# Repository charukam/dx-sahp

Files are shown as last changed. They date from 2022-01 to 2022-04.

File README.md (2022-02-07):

# Direct Expansion Solar Assisted Heat Pump
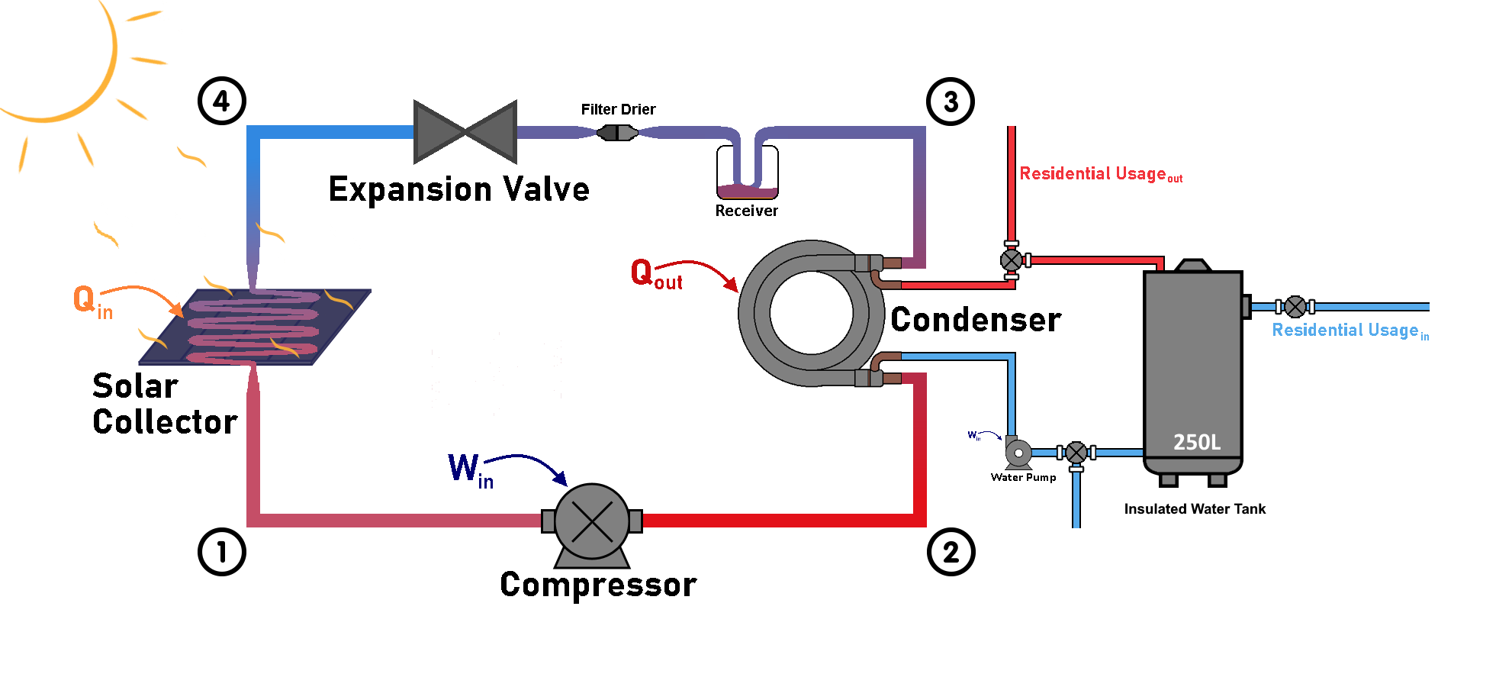
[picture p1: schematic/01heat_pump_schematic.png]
Heat Pump Cycle Schematic

Univeristy of Calgary Capstone Project creating a full scale heat pump cycle with a novel solar collector to heat a domestic hot water tank.

### MATLAB Code
_CoolProp_ (a C++ library) is required to run the MATLAB code to calculate system states for different refrigerants: http://www.coolprop.org/

### SOLIDWORKS Model
SOLIDWORKS 2020 is required for the SLDPRT and SLDASM files

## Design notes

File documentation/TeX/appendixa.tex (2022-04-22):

\chapter{Appendix A: Bill of Materials}

\begin{figure}[H]
    \centering
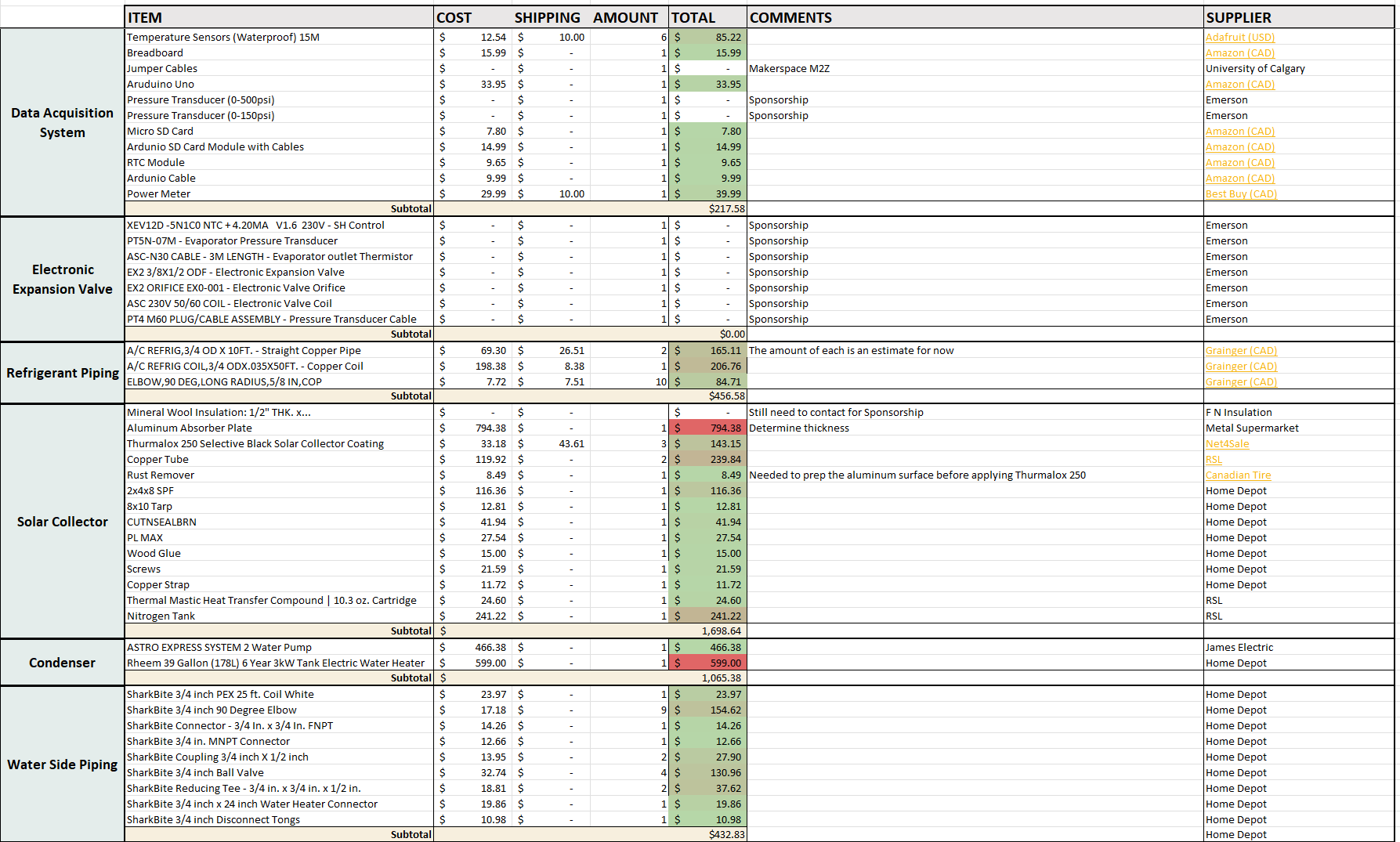
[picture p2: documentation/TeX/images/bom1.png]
    
\end{figure}
\begin{figure}[H]
    \centering
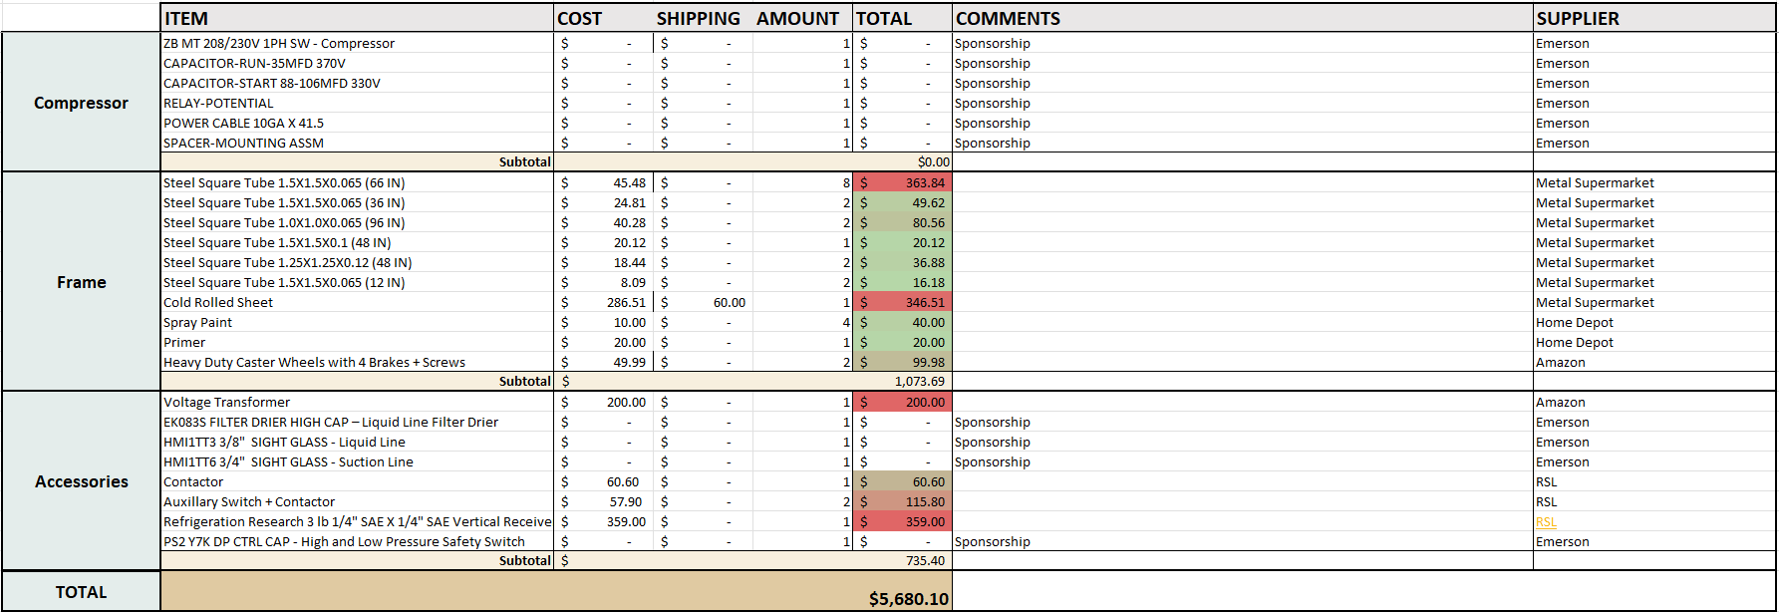
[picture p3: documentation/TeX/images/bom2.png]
    
\end{figure}

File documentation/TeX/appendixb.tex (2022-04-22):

\chapter{Appendix B: Gantt Chart}

\begin{figure}[H]
    \centering
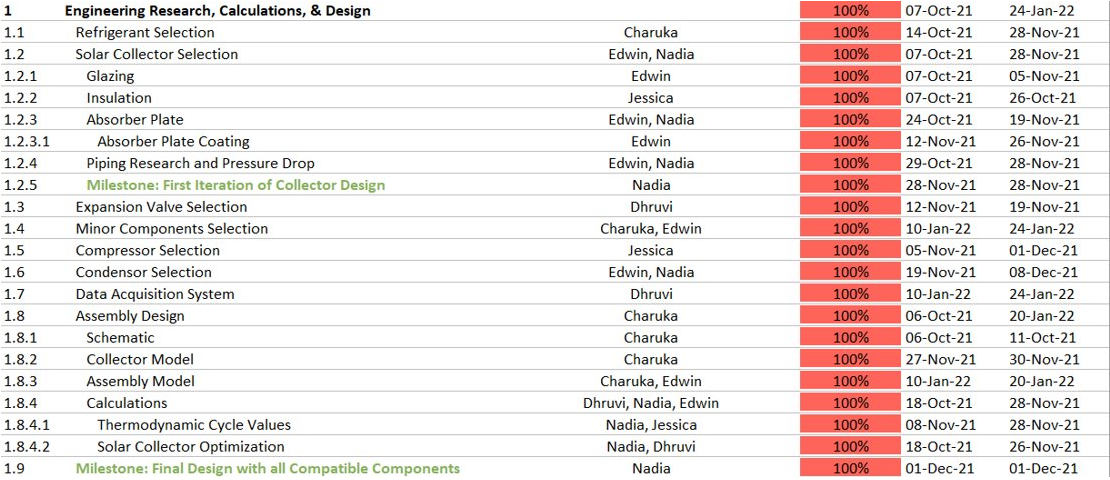
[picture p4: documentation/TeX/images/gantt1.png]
    
\end{figure}
\begin{figure}[H]
    \centering
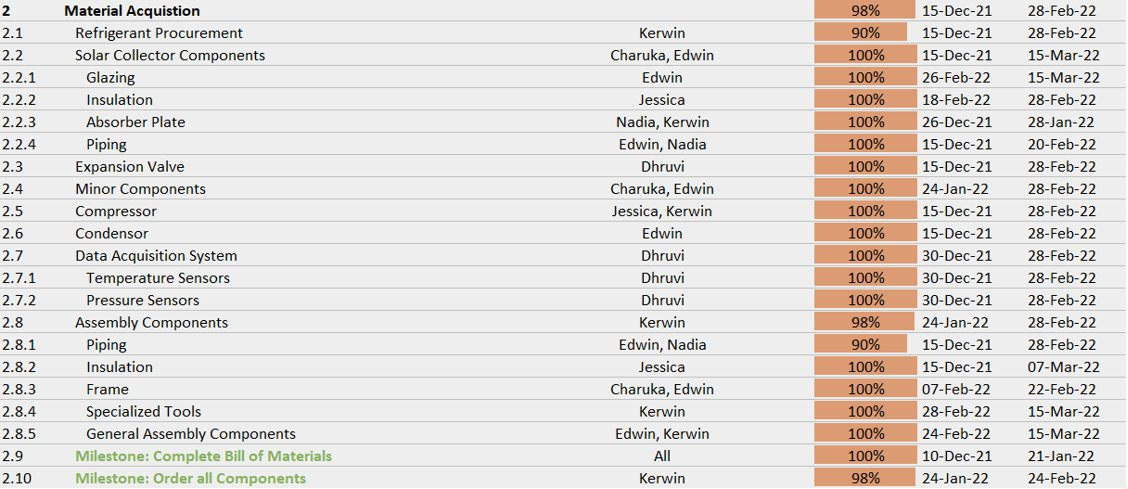
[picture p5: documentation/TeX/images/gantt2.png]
    
\end{figure}
\begin{figure}[H]
    \centering
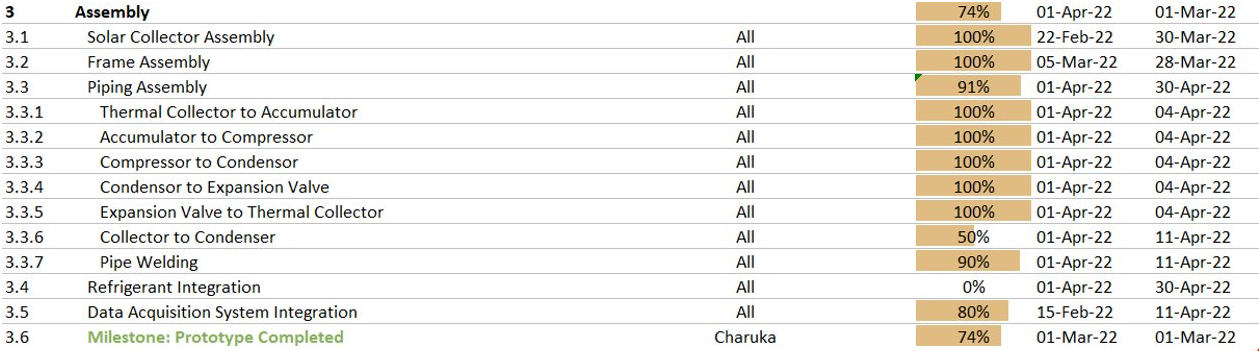
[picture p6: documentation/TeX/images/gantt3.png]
    
\end{figure}
\begin{figure}[H]
    \centering
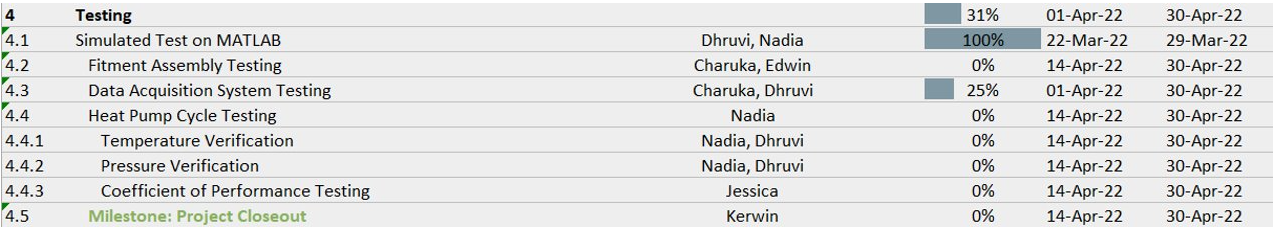
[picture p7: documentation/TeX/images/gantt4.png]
    
\end{figure}

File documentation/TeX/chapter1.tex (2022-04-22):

\chapter{Project Overview}

\section{Background and Motivation}

Climate change is a growing concern due to the effects that global warming has on the environment. As the population of the world increases, the energy demand will increase in turn. Due to the reliance on fossil fuels, this will only increase the amount of greenhouse gases that is produced into the atmosphere. This is why it is important to explore alternative energies that are relatively “greener” in comparison to the standard fossil fuels that are mainly used.

\medskip
A major sector where energy can be saved is domestic hot water heating. 19.3\% of the residential energy usage in Canada is from water heating \cite{water_heaters}. This statistic can be improved with the implementation of technology that uses other sources of energy to provide water heating. This project focuses on a Direct Expansion Solar Assisted Heat Pump (DX-SAHP), which is an example of a technology that can be used in place of natural gas for heating. The DX-SAHP combines the benefits of a heat pump with the abundance of solar energy that we receive.

\medskip
Unlike an Air Source Heat Pump (ASHP), the DX-SAHP uses a combination of solar energy and the ambient temperature to evaporate the refrigerant, improving the performance and making it viable for areas with a colder climate. The use of solar energy in conjunction with the heat pump reduces the amount of electricity that is needed for a standard heat pump to generate hot water.

\newpage
\begin{figure}[ht]
    \centering
    
    \caption{DX-SAHP Schematic}
\end{figure}
\medskip
The solar collector is what will be used instead of a traditional evaporator in the DX-SAHP. The collector is heated up, due to it being in direct sunlight, and thus it heats up and evaporates the refrigerant running below it. Ambient temperatures play a critical role in the performance of a heat pump with a solar collector. This is due to the solar collector directly being affected by how much irradiance, the amount of light striking a surface, is available. To design a collector for colder climates, where perhaps less irradiance is available, there must be key considerations that are considered. Additionally, other required components must be matched to the demand and to the solar collector size.

\section{Problem Statement}
The current state of heating in Alberta is overly reliant on natural gas and the technology that is currently being used to heat domestic water is contributing to the increase in global temperatures via greenhouse gas emissions. DX-SAHP can be used to phase out natural gas heaters by using the sun as an energy source instead. Therefore, a DX-SAHP can be designed that can heat an average household of 3 people within the Calgary region.

\section{Overview of Scope}
The goal of this capstone is to design a DX-SAHP that can heat 225L of domestic hot water to a household of 3 people. This number was calculated from the information from the Government of Canada stating that the average Canadian uses 75L of hot water a day \cite{water_heaters}. Knowing this, a DX-SAHP will be designed and manufactured. The effort will be mainly focused on optimizing the area of the collector while reducing the heat losses from convection and radiation. Component matching analysis and selecting a compatible compressor, condenser, and electronic expansion valve is necessary so that it is system functions properly. This heat pump must be equipped with all the necessary controls and data acquisition systems. Afterwards a working model will be made in order to be functional within Calgary and an economic and environmental analysis will be conducted to justify the proposed system.

\medskip
To determine the sizing of the DX-SAHP initial parameters must be set.

\medskip
Statistics Canada states that the average Canadian household occupies 2.47 members, and the average Canadian uses 75L of hot water per day \cite{stats_canada}. For the purposes of the DX-SAHP, it will be assumed that a domestic household of 3 people will require 225L of hot water per day. The hot water will be required to exit the system at a temperature of 50\textdegree C for residential use to avoid bacteria buildup in the water tank such as legionella. 

\medskip
The municipal water supply differs in temperature depending on the time of year. When it is winter, municipal line comes in at 10\textdegree C unlike in the summer when it comes in at 20\textdegree C. This is an important parameter to be considered when quantifying what heat load the heat pump will have to supply.

\medskip
To validate and maintain quantifiable design goals, the project will be considered successful if it is able to sustain 225L of water at 50\textdegree C while maintaining a coefficient of performance ($COP$) greater than 2.3. This means the DX-SAHP must be able to provide the following heat loads.

\smallskip
\begin{align}
    Q_L = 225L \times \frac{1000g}{1L} \times 4.18\frac{J}{g\SI{}{\celsius}}\times (\SI{50}{{\celsius}} - \SI{10}{{\celsius}}) = 37,620kJ
    \\\eqname{Heat Load Required during Winter Conditions}
\end{align}

\begin{align}
    Q_L = 225L \times \frac{1000g}{1L} \times 4.18\frac{J}{g\SI{}{\celsius}}\times (\SI{50}{\celsius} - \SI{20}{\celsius}) = 28,215kJ
    \\\eqname{Heat Load Required during Summer Conditions}
\end{align}

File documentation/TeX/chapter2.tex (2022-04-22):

\chapter{Conceptual Design}

\section{Background Research}

The most common water heater is the storage tank water heater. The way it functions is by heating up water that will be stored within a storage tank. This is most conventional since it is easy and cheap to install when comparing it to other water heaters. The limiting factor is that it is limited by the size of the storage tank. It may take a while for the hot water to be heated again if it runs out.

\medskip
Another type of water heater that is used is an Air Source Heat Pump (ASHP). What makes this heat pump unique is that it uses the heat within the air to heat the water. All it needs is a little bit of electricity to power the system. This makes the ASHP two to three times more efficient than most water heaters \cite{heat_pump_water_heaters}. The major drawback is that it needs to take heat from the air, therefore it is not suitable for basements or colder climates.

\begin{figure}[ht]
    \centering
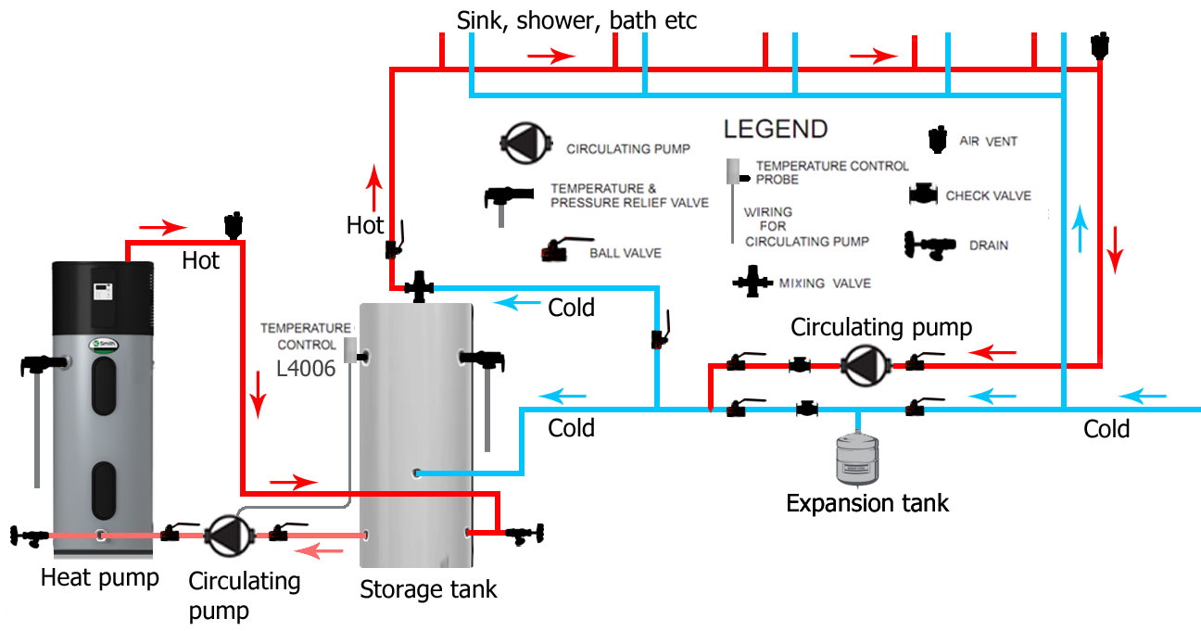
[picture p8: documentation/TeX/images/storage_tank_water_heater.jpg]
    \subfloat[\centering Storage Tank Water Heater {\cite{water_heater_img1}}] {{}}
    \qquad
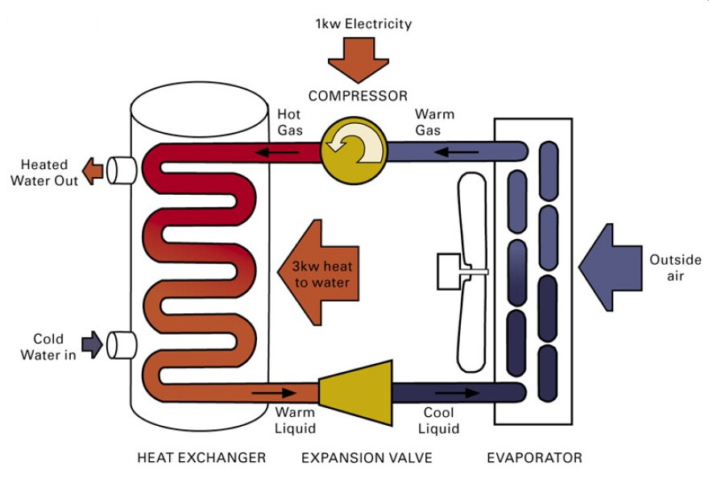
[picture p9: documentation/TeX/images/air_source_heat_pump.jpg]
    \subfloat[\centering Air Source Heat Pump Water Heater {\cite{water_heater_img2}}] {{}}
    \caption{Conventional Water Heaters}
\end{figure}

\smallskip
Unlike the ASHP, the DX-SAHP uses solar energy to provide the heat needed to heat the water. When comparing Figure 2.2 with Figure 1.1, a solar collector is used instead of an evaporator. This gives all the benefit of an Air Source Heat Pump with the additional benefit of working in colder climates since the sun can provide enough energy to heat the water.

\medskip
When designing a DX-SAHP, it is important to consider the irradiance available in the area. Irradiance is the amount of energy received from the sun within an area. As seen in Table 1, the amount of sun Calgary receives is drastically different between the winter and summer data sets.

\medskip
Winter months are defined from October to March in Table 2.1 while summer is between April to September. The justification behind choosing those date ranges is that it makes use of the entire year, and it is split between when Calgary has the most daylight hours versus the least. It also happens to line up with the solstices.

\medskip

\begin{table}[H]
\centering
\caption{Calgary Irradiance Data}
\rowcolors{2}{gray!20}{white}
\begin{tabular}{|P{10mm}|P{70mm}|P{70mm}|}
    \hline
    \rowcolor{orangeRed}
    Hour &  Average Winter Irradiance Data $(W/m^2)$ & Average Summer Irradiance Data $(W/m^2)$ \\
    \hline
    1 & 0 & 0 \\
    2 & 0 & 0 \\
    3 & 0 & 0 \\
    \cite{heat_pump_water_heaters} & 0 & 0 \\
    5 & 0 & 1.398907104 \\
    6 & 0 & 12.99453552 \\
    7 & 0.510989011 & 76.3715847 \\
    8 & 7.736263736 & 182.0710383 \\
    9 & 54.40659341 & 327.442623 \\
    10 & 149.6538462 & 445.6065574 \\
    11 & 229.7857143 & 557.2896175 \\
    12 & 289 & 612.0601093 \\
    13 & 316.7087912 & 629.9289617 \\
    14 & 301.6868132 & 587.7923497 \\
    15 & 252.4285714 & 539.8196721 \\
    16 & 178.3241758 & 474.3715847 \\
    17 & 86.85714286 & 374.3879781 \\
    18 & 29.04395604 & 252.4043716 \\
    19 & 3.708791209 & 142.9016393 \\
    20 & 0 & 44.86885246 \\
    21 & 0 & 4.256830601 \\
    22 & 0 & 0 \\
    23 & 0 & 0 \\
    24 & 0 & 0 \\
    \hline
\end{tabular}
\end{table}

\medskip
\section{Sponsor Requirements}
The sponsor's requirement for this capstone project was the design of a  DX-SAHP system that can satisfy the domestic hot water demand of the average Canadian household (~225L) of hot water per day \cite{stats_canada}.The system had to be disassemble, which was considered through the fabrication of a 3-part support frame, and through the incorporation of valves between the HVAC subcomponents. 

\medskip
\section{Collector Type Selection}

There are three types of solar collectors that are commonly used in the market; they are flat plate collectors, evacuated tube collectors, and concentrating collectors. Each comes with their own benefits and drawbacks.

\medskip
Flat plate collectors consist of a flat absorber plate that is orientated towards the sun. They use both direct and diffuse solar radiation and normally do not require a tracking system. Their main applications are solar water heating, heating for buildings, air conditioning and heat for industrial processes \cite{solar_thermal_energy}.

\medskip
In contrast, evacuated tube collectors consist of several rows of parallel transparent glass tubes which have the working fluid flowing within it. The glass tubes are cylindrical in shape which results in the sunlight always being perpendicular to the heat absorbing tubes. This is a major benefit since this collector can be used when the sun is low in the sky or on cloudy days and they are particularly useful in colder climates.

\medskip
Concentrating collectors are more suited for systems that require higher temperatures than what is achievable with a flat collector. The concentrating collector can be optimized by decreasing the area of heat loss when comparing it to flat plate collectors. This is done by placing an optical device between the source of radiation and the surface. A disadvantage that this technology has is that a sun tracking system is required to always maximize the incident radiation. This tracking system increases the overall cost of the collector and leads to additional maintenance which is why it was not considered at all for this project \cite{solar_thermal_energy}.

\medskip
When comparing flat plate collectors with evacuated tubes, there are several categories that can be considered. When comparing costs, evacuated tubes are around 10-15\% more expensive than flat plate. This was important to consider due to the limited budget that this project has \cite{flat_plate}. Another important area that needs to be looked at would be how the collector can handle snow. Since there will be no tracking system for our design, there will be no way to shake off the snow, so the collector must remove it passively. The benefit of a flat plate collector is that snow can shed easily unlike with evacuated tubes in which it can get stuck due to the tubes creating a strong vacuum \cite{flat_plate}.

\medskip
Both flat plate and solar collectors are excellent at heating water. The main question that needs to be asked when selecting the collector type is how much water needs to be heated to the desired temperature. Evacuated tubes are great for colder climates since they can heat water up to 121\textdegree C but it has the tendency to overheat. Therefore, evacuated tubes are more commonly used for commercial rather than domestic purposes. Unlike evacuated tubes, flat plate collectors can heat water up to 82\textdegree C which means that it is has smaller chance of overheating. This temperature range is suitable for domestic hot water usage \cite{flat_plate}.

\medskip
When looking at all the parameters, the flat plate collector was selected instead of the evacuated tube or concentrating collector. Although the evacuated tube collector works better in colder climates than the flat plate collector, it was excessive in terms of both cost and design work for domestic water heating. The flat plate satisfies many requirements for a collector in colder climates, and it is the recommended collector for domestic water heating \cite{flat_plate}. Therefore, for the design, the flat plate collector was chosen.

\section{Refrigerant Selection}

A refrigerant is a working fluid used in the thermodynamic cycle of a heat-pump, where the fluid will undergo multiple phase changes from liquid to vapor and vice versa, throughout the system cycle. One of the first components in a heat pump, which must be determined early on, is the refrigerant. To determine which components (i.e., compressor, condenser, and expansion valve) will be used in the DX-SAHP, the working fluid must be selected. Although there were many refrigerants to choose from, the list was drastically cut down after considering multiple criteria. These criteria looked at the environmental acceptability, safety, application, performance, and the economics associated with various refrigerants.

\medskip
The Ozone Depletion Potential (ODP) is a measure of a refrigerant’s ability to damage the ozone layer relative to CFC-11 with an ODP of 1. Emissions from CFC’s (chlorofluorocarbons), HCFC’s (hydrochlorofluorocarbons), and other synthetic chemicals which created an “ozone hole” over the South Pole \cite{ozone_layer} have led to the Montreal Protocol on Substances that deplete the Ozone layer \cite{odp} – a global agreement made to phase out ozone-depleting substances. For the DX-SAHP, only refrigerants with an ODP equal to zero were considered.

\medskip
The Global Warming Potential (GWP) is the next major criterion regarding environmental acceptability. This is a metric measuring the energy of emissions, which one ton of a specific gas will absorb relative to the emissions of one ton of carbon dioxide (\ch{CO2}) over a hundred-year period \cite{gwp}. For example, a refrigerant with a GWP of 1430 will have 1430 times the global warming potential of \ch{CO2} over 100 years. In 2016, the Kigali amendment was made to the Montreal Protocol \cite{montreal_protocol}, proposing a complete phase down of HFCs by 2047 due to their high global warming potential. Furthermore, the European Union \cite{hfcs} took action to place market prohibitions on gases with a GWP greater than 750 in air-conditioning systems by 2025. Therefore, the considered refrigerants had to have a GWP below 750.

\medskip
Refrigeration cycles have three distinct applications: high temperature (comfort conditioning), medium temperature (food refrigeration), and low temperature (transport refrigeration). Domestic water heating falls into high temperature comfort conditioning applications. The most widely used refrigerant in these applications has been R-134A and R-134A. Due to the high SEER (Seasonal Energy Efficiency Ratio) ratings of R-134A compared to other refrigerants, it, along with R-410A, has dominated the air conditioning market for components. However, due to R-134A’s high GWP of 1430, refrigerants with similar thermodynamic properties used as replacements for the eventual phase down of R-134A were explored.

\newpage
Following the ASHRAE Standard 34 refrigerant safety classification, most refrigerants in use currently pose a very low toxicity and flammability threat – giving an ASHRAE safety designation of A1. Following the ASHRAE Standard 34 \cite{ashrae_safety} refrigerant safety classification, most refrigerants in use currently pose a very low toxicity and flammability threat – giving an ASHRAE safety designation of A1. ASHRAE Standard 34 assigns refrigerants to two toxicity (A or B), and four flammability classes (1, 2, 2L, 3). The safety designations for refrigerants are as follows:

\begin{itemize}[itemsep=3mm, parsep=-1mm]
\item Class A (Low Toxicity)
    \begin{itemize}
        \item Occupational exposure limit is 400ppm or greater
    \end{itemize}
\item Class B (High Toxicity)
    \begin{itemize}
        \item Occupational exposure limit is less than 400ppm.
    \end{itemize}
\item Class 1 (No flame propagation)
    \begin{itemize}
        \item No flame propagation at 60\textdegree C and atmospheric pressure.
    \end{itemize}
\item Class 2L (Low flammability)
    \begin{itemize}
        \item Flame propagation at 60\textdegree C and atmospheric pressure.
        \item Lower Flammability Limit $> 0.10kg/m^3$ and Heat of Combustion $< 19,000 kJ/kg$
        \item Burning velocity <= 10cm/s at 23\textdegree C
    \end{itemize}
\item Class 2 (Flammable)
    \begin{itemize}
        \item Flame propagation at 60\textdegree C and atmospheric pressure.
        \item Lower Flammability Limit $> 0.10kg/m^3$ and Heat of Combustion $< 19,000 kJ/kg$
    \end{itemize}
\item Class 3 (High flammability)
    \begin{itemize}
        \item Flame propagation at 60\textdegree C and atmospheric pressure.
        \item Lower Flammability Limit $<= 0.10kg/m^3$ or Heat of Combustion $< 19,000 kJ/kg$
    \end{itemize}
\end{itemize}

\medskip
Because the system was designed for a residential water heating supply, only refrigerants designated in Class A toxicity were used due to possibility of leakage.

\medskip
As with many design considerations in engineering, there is an equivalent exchange when reducing the global warming potential of refrigerants. A general trend can be observed in refrigerants where a lower GWP equates to a higher flammability designation; most new generation refrigerants with a GWP less than 750 have an ASHRAE safety designation of A2L. While refrigerants of Class 1 are the most desirable, Class 2L refrigerants can also be considered safe \cite{low_gwp} to use in domestic heating systems as they have a high Minimum Ignition Energy and would need to be exposed to an open flame or high energy source with sufficient concentrations to ignite.

\medskip
Although each refrigerant will result in different system efficiencies, by looking at the critical temperature of the refrigerant, a correlation can be made for both the coefficient of performance and the cooling capacity of the system. As the critical temperature of the refrigerant increases, the coefficient of performance of the system is found to increase, while the cooling capacity is found to decrease \cite{low_gwp_options}. A higher coefficient of performance will ultimately result in a lower energy bill for the end user, while a lower cooling capacity will result in a larger system. As the project location is for a cold climate in Calgary, the refrigerant must also be chosen to have a freezing point, $T_{fp} < \SI{-50}{\celsius}$. Furthermore, CoolProp \cite{cool_prop} was used to conduct the thermodynamic analysis, and therefore, refrigerants of choice must be available on the database such that the system calculations can be performed.

\medskip
Finally, the economics and procurement of the refrigerants were considered where the system will require between 3-6 pounds of charge. After contacting vendors, many refrigerants were found to have more than 3 months lead times due to COVID-19 supply chain issues, and as a result would not satisfy the project’s timeline. Many new generation refrigerants were also found to be cost-ineffective when compared to their incremental performance benefits. These refrigerants ranged from \$400 to \$3000 per their minimum selling quantities.

\medskip
A design requirements table was then created to easily compare the refrigerants as seen below.

\medskip
\begin{table}[H]
\centering
\caption{Refrigerant Criteria}
\rowcolors{2}{gray!20}{white}
\begin{tabular}{|P{23mm}|P{23mm}|P{23mm}|P{23mm}|P{23mm}|P{23mm}|}
    \hline
    \rowcolor{orangeRed}
    Refrigerant &  ODP & GWP & Alternative To & Safety Class & $T_{critical}$ (\textdegree C) \\
    \hline
    R-410A           & 0 & 2088 & R-22   & A1  & 72.13 \\
    R-717 (\ch{NH3}) & 0 & 0    & R-22   & B1  & 132.4 \\
    R-1234yf         & 0 & 4    & R-134A & A2L & 94.70 \\
    R-1234ze         & 0 & 1    & R-134A & A2L & 109.4 \\
    R-32             & 0 & 675  & R-410A & A2L & 78.40 \\
    R-454B           & 0 & 466  & R-410A & A2L & 78.10 \\
    R-454C           & 0 & 148  & R-410A & A2L & 82.40 \\
    R-455A           & 0 & 146  & R-410A & A2L & 86.60 \\
    R-466A           & 0 & 733  & R-410A & A1  & 76.50 \\
    R-515B           & 0 & 299  & R-134A & A1  & 108.7 \\
    R-290            & 0 & 3    & R-410A & A3  & 97.00 \\

    \hline
\end{tabular}
\end{table}

\medskip
After assessing these criteria, and contacting supply vendors, it was determined that R-32 was preferred refrigerant for the  DX-SAHP system. The decision was contingent upon the refrigerant’s suitability with the team’s initial selection criteria. With a zero ODP, a GWP less than 750, a critical temperature of 78.4\textdegree C, but most importantly, a procurement time of 2 months, the R-32 was determined to be the appropriate working fluid.

\medskip
Upon determination of R-32 as the working fluid for the system, the component matching phase began. Although some components were found for this refrigerant (e.g., expansion valve), when looking for a compressor compatible with R-32, and which could be procured within a reasonable time frame, component matching proved to be difficult.

\medskip
After consulting with a subject matter expert working in the heating ventilation and cooling (HVAC) sector for over 15 years, the team determined the reason for the difficulties to be that R-32 and all other similar new generation refrigerants are still considered novel to the industry. As R-134A is still dominating the air conditioning industry in North America, components for comfort cooling heat pump applications are designed around R-134A being the working fluid. However, the research was not in vain; since R-32 is the widespread refrigerant of choice in Asia and is slowly being phased in around parts of Europe as the next replacement for high GWP refrigerants, it is beneficial to have considered it as a potential working fluid for the DX-SAHP.

\medskip
Finally, although the GWP was far too high, it was still suggested to design the system using R-134A as North America has not yet caught up with the refrigerant phase down plan. Furthermore, the use of R-134A as a system refrigerant is not detrimental to the project’s environmental considerations as the final solution to avoid the use of a high GWP refrigerant is through sourcing drop-in replacements. A drop-in replacement for R-134A (such as HFO-1234yf) is a refrigerant which can simply swap R-1234yf while maintaining the same system components. This allows for the system calculations, and thus, the system components to be modeled and procured based upon R-134A as the working fluid. The advantage of taking the approach of using drop-in refrigerants is that, as new refrigerants become available, supply chain delays would not hinder the progress of the build assembly as R-134A could always be used to complete the project.

\section{HVAC Components}

\subsection{Compressor Type Selection}

For the purposes of the compressor in the DX-SAHP system, a hermetic sealed variable speed compressor was initially selected. This type of compressor operates via positive displacement and can achieve higher compression ratios per single stage of compression \cite{other_compressors}. Additionally, they are more compact and less prone to vibration.

\medskip
Hermetic compressors are widely used in domestic refrigeration systems wherein continuous maintenance cannot be ensured by the user. A hermetic compressor consists of the compressor part directly mounted on the shaft of the motor. The compressor and motor are confined together within an outer shell, reducing the potential for dust particles to access the interior and consequently impact the operation of the compressor \cite{hermetic_compressors}. With both the compressor and motor being directly coupled on the same shaft and confined within a common casing, the potential for leakage of R-134A is essentially eliminated \cite{what_hermetic_compressor}. The hermetic compressors investigated for the purpose of the DX-SAHP system were of the reciprocating and rotary types.

\medskip
The variable speed aspect of the compressor is facilitated by the adjustability of the motor speed in response to shifting power demands, thereby conserving energy. For the purposes of this analysis, the ability to control the speed of the compressor allows for the control of the pressure differential of the refrigerant, R-134A. Previously, it was considered essential to control the varying conditions at the compressor inlet to obtain a quasi-constant condensation temperature of 60\textdegree C. 

\medskip
However, due to the complexities associated with variable speed compressors such as capacity incompatibility, refrigerant incompatibility, as well as the elevated complexity of utilizing 3-phase motor capable of supporting the integration of a variable frequency drive, it was decided that a single speed compressor would be more adequate.

\medskip
Among the many choices for compressors depicted in Figure 2.2, the following design alternatives for a hermetic variable speed compressor have been taken into consideration, allowing for use in domestic water heating applications \cite{how_compressor_works} \cite{vapor_compression_refrigeration}.

\medskip
\begin{enumerate}[itemsep=3mm, parsep=-1mm]
    \item Scroll variable speed compressor \cite{scroll_compressors}
    \item Reciprocating variable speed compressor \cite{variable_speed_hermetic}
    \item Rotary screw variable speed compressor
    \item Centrifugal variable speed compressor
    \item Open motor hermetic speed compressor
\end{enumerate}

\medskip
The following figure shows common compressors and their classification.

\medskip
\begin{figure}[ht]
    \centering
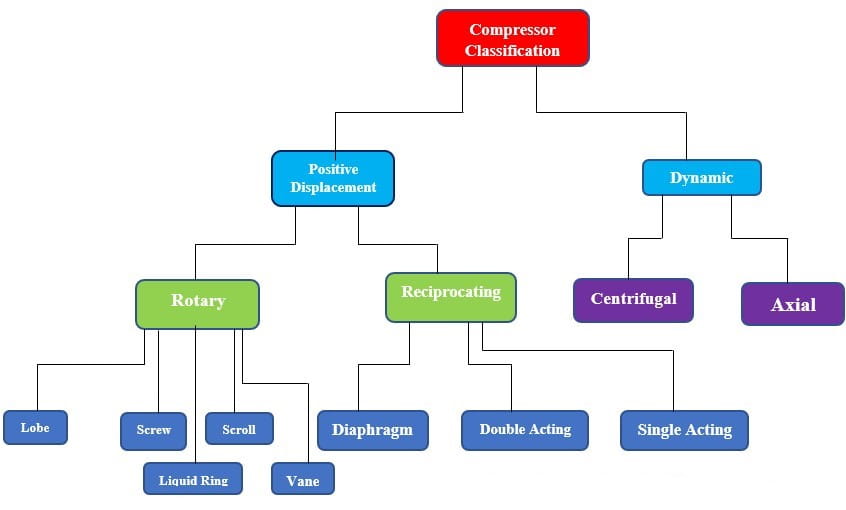
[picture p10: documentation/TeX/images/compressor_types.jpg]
    
    \caption{Compressor Classification \cite{air_compressor}}
\end{figure}

\medskip
Out of the five listed compressors, the suitable design alternative was found to be the scroll compressor as it offers the following design-specific benefits:

\medskip
\begin{enumerate}[itemsep=3mm, parsep=-1mm]
    \item lower compressor power ratings.
    \item compatible with R-134A.
    \item single phase.
    \item operate within the operating pressures of the system design parameters.
    \item operate within the evaporating temperature ranges of the system design parameters.
    \item have low sound and vibrations.
    \item longer compressor life.
    \item reduces leak potential.
    \item exhibit energy saving capabilities \cite{scroll_compressor} \cite{what_scroll_compressor}.
\end{enumerate}

\medskip
Notwithstanding, the rotary screw and reciprocating positive displacement variable speed compressors may also be used for the purposes of the DX-SAHP. However, since rotary screw compressors are more commonly used in commercial and industrial applications, they are not the most suitable alternative. Contrastingly, reciprocating compressors are commonly used in residential applications; however, they were not the preferred option due to their loud noise, limited speed and the tendency for their piston ring to wear and reduce their efficiency.

\medskip
A centrifugal type of compressor was also not the preferred alternative since these compressors are often used in industrial applications, large chillers, refineries, and plants \cite{centrifugal_compressor}. Therefore, they operate at a much higher horsepower and for higher operating pressures than required for the purpose of the DX-SAHP. Finally, the open motor variable speed hermetic compressor is not suitable as it presents a higher risk of refrigerant leakage than a sealed hermetic variable speed compressor or scroll compressor does.

\subsection{Condenser Type Selection}

Storage tank water heaters are by far the most prevalent configuration of water heaters available on the market today; however, tankless or “On-Demand” water heaters are slowly acquiring some of that market share due to their reputation of running more efficiently. For the purposes of selecting a condenser/water storage tank for the Direct Expansion Solar Assisted Heat Pump, the team considered the following factors:

\medskip
\begin{enumerate}[itemsep=3mm, parsep=-1mm, label=\roman*.]
    \item The operational time span of the evaporator/collector.
    \item The stability of meteorological conditions of the design locale.
    \item The temperature of the inlet municipal water supplied for domestic use.
\end{enumerate}

\medskip
By relying on weather station data from the Government of Canada \cite{climate_summary}, we determined the average, daily “bright sunshine hours”, to be 4.68 hours for Calgary during the winter season. These hours would support peak operation of the Solar Thermal Collector, and outside of which, the system performance may decline, and in extreme conditions, stagnate, ceasing the supply of hot domestic water in the absence of a suitable thermal mass. Assessing the stability or consistency of the meteorological conditions, such as ambient temperatures and average irradiance, the team concluded that the short operational time frame, paired with the instability of meteorological conditions and potential for inclement winter weather conditions, such as extreme subzero temperatures and collector shading due to snowfall, the DX-SAHP cannot support a tankless water heater module as a steady supply of hot water would not be guaranteed outside of optimal operational conditions. Furthermore, considering that the temperature of the supplied groundwater determines the length of the heating period in a tankless water heater, and that inlet municipal water is supplied at approximately 10\textdegree C during the winter, adopting a tankless water heater is not a feasible option for this application due to prolonged heating times. In conclusion, the team opted to adopt a coaxial condensing coil-style condenser well as an insulated water tank, which acts as a thermal mass from which emergency supply of hot water could be provisioned. Further selection considerations are highlighted in section 3.3.2 below.

\subsection{Expansion Valve Selection}

An electronic expansion valve was selected as the throttling valve in the DX-SAHP system. Throttling valves allow control of the amount of mass flow rate by adjusting the size of the flow path through the valve. The two types that were initially compared were the thermostatic valve (TXV) and the electronic expansion valve (EXV). 

\medskip
TXV’s typically use sensing bulbs to sense the temperature of the suction line. These bulbs are slightly warmer than the saturation temperature of the refrigerant and have an increase in pressure when the suction line temperature exceeds the saturation temperature. The increased pressure in the bulb indicates that more refrigerant is required to manage the system’s evaporating heat load. The opening of the valve occurs by the internal connections from the bulb to the power element. The power element consists of a diaphragm and with increasing pressure, the diaphragm is bent downwards to open the valve.

\medskip
EXV’s use an electronic controller to calculate the superheat based on the temperature and pressure at the suction line, and the outlet of the solar flat plate collector. For the controller to read the pressure and temperatures, respectively, pressure transducers and thermistors may be used. The programming of the controller controls the valve movement by either opening or closing the valve, based on the inputs read by the sensors.

\medskip
The main disadvantages of using a TXV is that if the pressure differential between the sensing bulb, combined pressure below the diaphragm, and the spring are significantly reduced, the opening and closing of the valve will be affected. Ultimately, this creates a problem for the system to operate as efficiently, mainly on the release of the mass flow rate as required for the heating load.

\medskip
Based on this, the EXV was selected as the throttling valve to be placed in the system. EXV’s offer more flexibility for system design requirements by having the ability to use the controller without needing to physically adjust the valve.

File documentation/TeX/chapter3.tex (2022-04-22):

\chapter{Design Development}

\section{Collector Engineering Analysis}

\subsection{Heat Transfer Analysis}

To model the heat transfer, depicted in Figure 3.1, occurring on the surfaces of a flat plate collector, the following simplifications were made:

\medskip
\begin{itemize}[itemsep=3mm, parsep=-1mm]
    \item Performance is steady state. 
    \item Heat losses through the front and back are to the same ambient temperature.
    \item Construction is of the sheet and serpentine manifold type.
    \item Uniform flow exists within the tubes.
    \item Absorption of solar energy by the cover is insignificant insofar as it affects losses from the collector. 
    \item Temperature drop through the cover is negligible. 
    \item Heat flow through the cover is one-dimensional.
    \item The cover is opaque to infrared radiation. 
    \item Heat flow through the back insulation is one-dimensional. 
    \item The sky is considered a black body for long-wavelength radiation at the equivalent sky temperature.
    \item Temperature gradients around the tubes are negligible. 
    \item Properties of the collector are independent of temperature. 
    \item Dust, dirt, and snow buildup on the collector are negligible. 
    \item Shading of the collector absorber plate is negligible.
\end{itemize}

\medskip
\begin{figure}[H]
    \centering
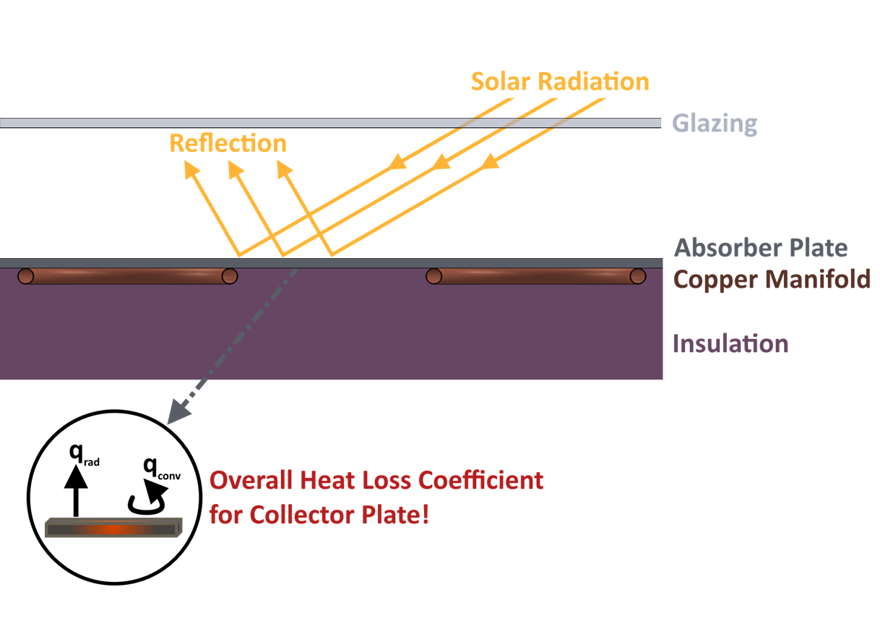
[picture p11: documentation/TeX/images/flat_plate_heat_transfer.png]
    
    \caption{Heat Transfer from a Flat Plate Collector}
\end{figure}

\medskip
The heat losses were analytically simplified by characterizing them using the thermal network depicted in Figure 3.2a. An equivalent thermal network, as shown in Figure 3.2b, can then be deduced to encompass the overall steady-state heat transfer occurring across the collector. The heat transfer analysis is derived in full detail below.

\smallskip
\begin{figure}[H]
    \centering
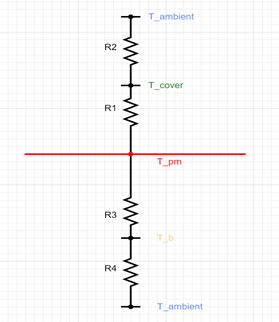
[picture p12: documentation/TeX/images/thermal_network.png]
    \subfloat[\centering One-Cover Flat-Plate Collector] {{}}
    \qquad
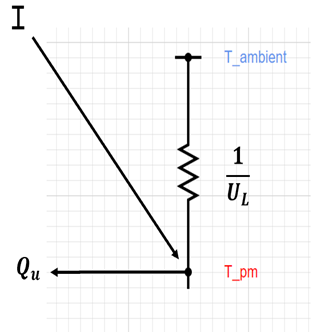
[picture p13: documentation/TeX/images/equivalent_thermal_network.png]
    \subfloat[\centering Equivalent Thermal Network] {{}}
    \caption{Thermal Network Diagrams}
\end{figure}

\medskip
First, the top heat losses, both convective and radiative, from the absorber plate to the cover were  evaluated as follows to determine the first thermal resistance, R1:
\begin{align}
    Q_{loss, top} = h_{c, p-c}(T_{pm}-T_c) + \ddfrac{\sigma(T^4_{pm}-T^4_c)}{\frac{1}{\varepsilon_p} + \frac{1}{\varepsilon_c} - 1}
\end{align}

\begin{align}
    h_{r, p-c} = \ddfrac{\sigma(T_{pm}-T_c)(T^2_{pm}-T^2_c)}{\frac{1}{\varepsilon_p} + \frac{1}{\varepsilon_c} - 1}
\end{align}

\begin{align}
    R1 = \ddfrac{1}{h_{c, p-c} + h_{r, p-c}}
\end{align}

\bigskip
Similarly, the top heat losses, both convective and radiative, from the cover to the ambient were evaluated as follows to determine the second thermal resistance, R2:
\begin{align}
    h_{r,c-a} = \ddfrac{\sigma\varepsilon_c (T_c + T_{sky})(T_c^2 + T_{sky}^2)(T_c - T_{sky})}{(T_c - T_a)}
\end{align}

\begin{align}
    R2 = \ddfrac{1}{h_w + h_{r,c-a}}
\end{align}

\bigskip
Finally, the total top heat loss coefficient, $U_{top}$, was found to be the inverse of the summation of R1 and R2 as follows:
\begin{align}
    U_{top} = \ddfrac{1}{R1 + R2}
\end{align}

\bigskip
A useful empirical equation for $U_{top}$ was developed by Klein (1979) following the basic procedure of Hottel and Woertz (1942) and Klein (1975). This relationship fits the graphs for $U_{top}$ for mean plate temperatures between ambient and 200\textdegree C to within $\pm 0.3 W/m^2 K$ and is represented below:
\begin{align}
    U_{top} = U_{tC} + U_{tR}
\end{align}

The heat loss through convective effects, $U_{tC}$, was quantified as: 
\begin{align}
    U_{tC} = \left[  \ddfrac{M}{\left(\frac{c}{T_{pm}}\right) \left( \frac{T_{pm} - T_a}{M+f} \right)^e} + \ddfrac{1}{h_w} \right]^{-1}
\end{align}

\bigskip
Where:
\begin{align}
    f   &= (1 + 0.089h_w - 0.116h_w \varepsilon_p)(1 + 0.07866N)\\
    e   &= 0.43 \left( 1 - \ddfrac{100}{T_{pm}}\right)\\
    c   &= 520 (1 - 0.000051\beta^2)\\
    h_w &= 5.7 + 3.8V_w
\end{align}

\bigskip
The heat loss through radiative effects, $U_{tR}$, was quantified as:
\begin{align}
    U_{tR} = \ddfrac{\sigma (T_{pm}^2 + T_a^2) (T_{pm} + T_a)}{(\varepsilon_p + 0.059Mh_w)^{-1} + \frac{2M + f - 1 + 0.133\varepsilon_p}{\varepsilon_g} - M}    
\end{align}

\bigskip
Therefore:
\begin{align}
    U_{top} = \left[  \ddfrac{M}{\left(\frac{c}{T_{pm}}\right) \left( \frac{T_{pm} - T_a}{M+f} \right)^e} + \ddfrac{1}{h_w} \right]^{-1} + \ddfrac{\sigma (T_{pm}^2 + T_a^2) (T_{pm} + T_a)}{(\varepsilon_p + 0.059Mh_w)^{-1} + \frac{2M + f - 1 + 0.133\varepsilon_p}{\varepsilon_g} - M}
\end{align}

\bigskip
R3 represents the resistance to heat flow through the insulation while R4 represents the convection and radiation resistance to the environment. With appropriate back insulation, it is usually possible to assume R4 is zero and all resistance to heat flow is due to the insulation.

\medskip
The heat loss through the bottom, $U_b$, of the collector can be defined as:
\begin{align}
    U_{bottom} = \frac{1}{R} = \frac{\delta_1}{k_1}
\end{align}

The heat loss through the sides, $U_{edge}$, of the collector can be defined as:
\begin{align}
    U_{edge} = \ddfrac{Q_{edge}}{A(T_{pm} - T_a)}
\end{align}

\medskip
Where:
\begin{align}
    Q_{edge} = A_p(T_{pm} - T_a)
\end{align}

\bigskip
The total heat loss coefficient is the sum of the heat loss coefficients for the top, bottom, and sides of the collector. It can be defined as:
\begin{align}
    U_L = U_{top} + U_{bottom} + U_{edge}
\end{align}

\begin{align}
    U_L = \left[  \ddfrac{M}{\left(\frac{c}{T_{pm}}\right) \left( \frac{T_{pm} - T_a}{M+f} \right)^e} + \ddfrac{1}{h_w} \right]^{-1} + \ddfrac{\sigma (T_{pm}^2 + T_a^2) (T_{pm} + T_a)}{(\varepsilon_p + 0.059Mh_w)^{-1} + \frac{2M + f - 1 + 0.133\varepsilon_p}{\varepsilon_g} - M}\nonumber\\
    + \frac{\delta_1}{k_1} + \ddfrac{Q_{edge}}{A(T_{pm} - T_a)}
\end{align}

\bigskip
Finally, the total useful heat gain of the collector was quantified as:
\begin{align}
    Q_u = F'A_c\left[ I(\uptau_c \alpha_c) - U_L(T_{fi} - T_a) \right]
\end{align}

\bigskip
The fin efficiency represents the efficacy with which energy absorbed by the abosrber plate and the tube spacing (conceptualized as fins) is collected on the sides of the tubes for subsequent heat transfer into the working fluid:
\begin{align}
    F = \ddfrac{tanh \left[ \ddfrac{m(W-D)}{2}\right]}{\left[ \ddfrac{m(W-D}{2}\right]}
\end{align}

\newpage
Where:
\begin{align}
    m = \sqrt{\ddfrac{U_L}{k_p\delta_p}}
\end{align}

\bigskip
Physically, $F'$, the collector efficiency factor, represents the ratio of the actual useful energy gain to the useful gain that would result if the collector absorbing surface had been at the local fluid temperature. It is essentially a constant for any collector design and fluid flow rate.
\begin{align}
    F' = \ddfrac{\frac{1}{U_L}}{W\left[ \frac{1}{U_L (D + (W-D)F)} \right] + \frac{1}{C_b} + \frac{1}{\pi D_i h_{fi}}}
\end{align}

\bigskip
The collector heat removal factor is a quantity that relate the actual useful energy gain of the collector to the useful energy gain has the entire collector surface were at the fluid inlet temperature. 
\begin{align}
    FR = \ddfrac{mC_p}{A_c U_L}\left[ 1-\exp\left( \frac{-A_c U_L F'}{mC_p}\right)\right]
\end{align}

\bigskip
It’s important to note that, as the mass flow rate through the collector increases, the temperature rise through the collector decreases. This corresponds to lower losses as the average collector temperature is lower, leading to an increase in the useful energy gain. This increase is reflected by an increase in the collector heat removal factor $FR$ when the mass flow rate increases.

\subsection{Collector Efficiency}

The collector’s instantaneous efficiency is defined as the ratio of useful heat energy gain to total energy incident on the collector’s surface:
\begin{align}
    \eta = \frac{Q_u}{I A_c}
\end{align}

\bigskip
The day-long collector efficiency is the summation of instantaneous efficiencies at known time steps, in our case, on an hourly basis:
\begin{align}
    \eta_{day} = \frac{\sum Q_u}{\sum I A_c}
\end{align}

\bigskip
As seen in the equations above, the absorber plate’s mean temperature is important in determining the values evaluated by the previous governing equations. With many unknowns, this value can only be determined through an iterative solution approach using an initial guess for the plate mean’s temperature. For our purposes, an initial guess of $T_{pm} = T_{fi} + 5$ is reasonable \cite{solar_energy_thermal_process}. Following the iterative algorithm described in the 'Code Logic' below, and summarized in Figure 3.4, the equation below can be used to determine a convergent solution for the final mean temperature of the plate:
\begin{align}
    T_{pm} = T_{fi} + \ddfrac{\frac{Q_u}{A_c}}{FRU_L} (1 - FR)
\end{align}

\subsection{Thermodynamic Cycle Analysis \& Collector Efficiency Optimization}

In thermodynamics, heat pump cycles are bound by two reservoir temperatures, namely, the evaporation and the condensation temperatures. For the purposes of the system, the condensation temperature is regarded as a set point: since the system is designed to support an outlet water temperature of 55\textdegree C for domestic use, $T_{cond}$ is constrained to be approximately 60\textdegree C. Determining the optimal, steady state evaporation temperature on which to base the collector design is key, not only to optimizing the flat plate collector’s area, but also to minimizing the radiative and convective heat losses emanating from its surfaces. Closely tied to the ambient temperatures, the evaporation temperatures of the working fluid circulating within the collector’s manifold dictate the useful heat gain of the collector or, more specifically, the efficiency of the collector, and correspondingly, the $COP$ of the overall system. Referring to ASHRAE’s heat pump \& air conditioning design conditions for Calgary, an initial range of design evaporation temperatures between -10\textdegree C and 10\textdegree C was selected.

\medskip
Additionally, meteorological data sets encapsulating average, hourly, winter-day temperatures and Irradiance values were loaded into the MATLAB \cite{MATLAB} file. Using a C++ Fluid Properties’, MATLAB-accessible library, CoolProp \cite{cool_prop}, the thermodynamic states of the Refrigerant R134A, including temperatures, pressures, enthalpy, and entropy, were determined for points 1 through 4 of the thermodynamic cycle. As depicted in Figure 3.3, the isobar between on which states 2-3 lie represents the set, saturation pressure corresponding to the design condensation temperature of 60\textdegree C. The collection of dashed isobars on which states 4-1 lie correspond to the saturation pressures of the chosen range of evaporation temperatures to undergo analysis. To simplify the analysis, the following assumptions of the thermodynamic cycle were made:

\begin{enumerate}[itemsep=3mm, parsep=-1mm, label=\roman*.]
    \item Constant pressure heat addition occurs in the collector.
    \item Constant pressure heat rejection occurs in the condenser.
    \item Isentropic compression occurs between states 1-2 in the compressor.
    \item Isenthalpic expansion occurs between states 3-4 in the expansion valve.
    \item The refrigerant enters the compressor at a quality of 1 or in a saturated vapor state.
\end{enumerate}

\medskip
These assumptions will later be corrected for thorough accounting for sub-component efficiencies as well as pressure drop in the collector.

\medskip
\begin{figure}[H]
    \centering
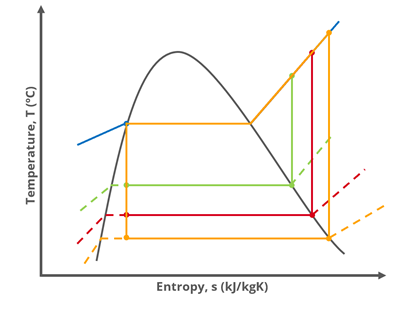
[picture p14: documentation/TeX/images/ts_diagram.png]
    
    \caption{T-s Diagram for Probable Design Evaporation Temperatures}
\end{figure}

\medskip
Using CoolProp [18], the team determined the performance parameters of the isolated heat pump cycle, namely, $Q_L$, $Q_H$, $W_{comp}$ and $COP$. With $W_{comp}$  or theoretical compressor work in mind, appropriate sizing for the compressor was determined. Next, code was developed which amalgamated the flat plate collector’s governing equations and, through iteration, allowed for the determination of the flat plate’s mean temperature. Figure 3.4 below depicts the complete iteration algorithm utilized in the MATLAB code.

\medskip
\begin{figure}[H]
    \centering
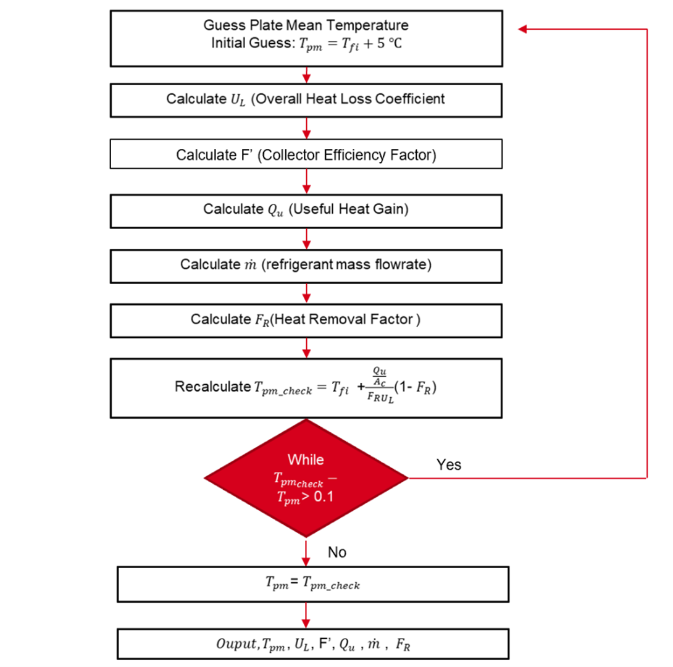
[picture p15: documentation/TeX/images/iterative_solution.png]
    
    \caption{Iterative Solution for Flat Plate Mean Temperature}
\end{figure}

\medskip
Once the flat plate’s mean temperature was determined, the collector’s useful heat gain, and, subsequently, the collector’s efficiency was evaluated for every data point in the evaporation temperature range. The evaporation temperature’s impact on the isolated heat pump cycle $COP$ is diametrically opposed to its impact on the useful heat gain of the collector: on one hand, the $COP$ of the heat pump cycle increases as the gap between the evaporation and condensation reservoir temperature is minimized, or when the chosen evaporation design temperature is elevated. On the other hand, the collector’s efficiency declines with the elevation of evaporation temperature as a result of increased heat losses from its surfaces. Noting this inverse relationship, it’s deducible that a plot of the product of $COP$ and Collector Efficiency (a quantity defined as the overall system $COP$) versus evaporation temperature would exhibit a characteristic inflection point at the evaporation temperature that maximizes both these inversely related parameters. For the DX-SAHP, the inflection point was seen to occur at -2\textdegree C. Knowing the design evaporation temperature, the team was able to subsequently determine the predicted collector efficiency, and the predicted useful, net collected heat. These values will later be leveraged to evaluate the theoretical performance of the DX-SAHP against the logged experimental performance. Using the code, the team also determined the system’s necessary flow rate, which supplemented the selection process of the remaining sub-components of the heat pump cycle.

\subsection{Insulation Selection}

Insulation is one of the most efficient ways to save energy by reducing heat loss during winter and thus lowering energy bills \cite{insulation}. Reducing heat loss in the collector means the compressor will have to do less work to meet the hot water requirements. For the flat plate collector, it was essential to investigate the concepts pertaining to location of any heat losses to the surroundings, type, thickness, and cost of insulation.

\medskip
In the solar flat plate collector, heat losses occur through the absorber plate by top losses. As the plate heats up, some of this heat is then transferred to R-134A (within the copper tubing of the collector that is bonded to the rear side of the aluminum absorber plate), while some of the heat is lost to the surroundings. The heat losses occurring through the back, and sides of the collector are respectively known as bottom and edge losses \cite{heat_losses}. From heat transfer and thermodynamic contexts, it is understood that these heat losses occur in the form of conduction, convection, and radiation as described in the sections above.\cite{heat_losses}.

\medskip
Based on the engineering analysis and design of the collector, the bottom and sides require insulation as to minimize any heat losses and the consideration of an insulation cover being required in case of probable exposure area that is responsible for the occurrence of any heat losses.

\medskip
The insulation materials representative of some of the materials commonly used in solar flat plate collectors and in the industry are as follows:

\medskip
\begin{itemize}[itemsep=3mm, parsep=-1mm]
    \item Fiberglass wool. 
    \item Rigid polyurethane foam.
    \item Mineral wool.
    \item Expanded polystyrene.
    \item Extruded polystyrene.
\end{itemize}

The following table represents the range of thermal conductivity values, temperature, and R-values \cite{thermal_insulation} for the mentioned types of insulation materials.

\medskip
\begin{table}[H]
\centering
\caption{Range for Thermal Conductivity, Temperature, and R-Value for Insulation}
\rowcolors{2}{gray!20}{white}
\begin{tabular}{|P{40mm}|P{35mm}|P{35mm}|P{35mm}|}
    \hline
    \rowcolor{orangeRed}
    Insulation Type & Thermal Conductivity, k $[W/mK]$ & Temperature Range & R Value [per inch of thickness] \\
    \hline
    Fiberglass Wool         & 0.023 - 0.040 & -195\textdegree C to 230\textdegree C & R-3.7 to R-4.2  \\
    Rigid Polyurethane Foam & 0.020 - 0.035 & 62\textdegree C to 93\textdegree C    & R-3.4 to R-6.7 \\
    Mineral Wool            & 0.033 - 0.040 & Maximum: 649\textdegree C             & R-3.7 to R-4.3 \\
    Expanded Polystyrene    & 0.030 - 0.040 & Maximum: 75\textdegree C              & R-3.9 to R-4.7 \\
    Extruded Polystyrene    & 0.025 - 0.040 & Maximum: 74\textdegree C              & R-5.0 to R-5.6 \\
    \hline
\end{tabular}
\end{table}

\medskip
The following table identifies the American Society for Testing and Materials (ASTM) specification, material type, and/or grade for some of the insulation materials that are commonly used in the industry \cite{insulation_design}.

\medskip
\begin{table}[H]
\centering
\caption{Common Types of Insulation - Based on ASTM}
\rowcolors{2}{gray!20}{white}
\begin{tabular}{|P{50mm}|P{50mm}|}
    \hline
    \rowcolor{orangeRed}
    Material & Insulation Standard \\
    \hline
    Cellular Glass   & ASTM C 552 Type II        \\
    Elastomeric      & ASTM C 534 Type I, Gr 1   \\
    Fiberglass       & ASTM C 547 Type I         \\
    Flexible Aerogel & ASTM C 1728 Type I, Gr 1B \\
    Phenolic         & ASTM C 1126 Type III      \\
    Polyethylene     & ASTM C 1427 Type I, Gr1   \\
    Polyisocyanurate & ASTM C 591 Type IV        \\
    Polystyrene      & ASTM C 578 Type XIII      \\
    \hline
\end{tabular}
\end{table}

\medskip
Based on the above analysis, mineral wool was selected as the insulating material to be used for the solar flat plate collector due to its excellent thermal properties. The mineral wool insulation was sponsored by Frank of FN Insulations. 

\medskip
Mineral wool has low thermal conductivity values, allowing for less heat to be passed through and lost to the surroundings. The suitable temperature range allows for use up to 649\textdegree C as this material will not melt until temperatures reach beyond 1,000\textdegree C. The R-values are within a range of R-3.7-R-4.3, allowing for it to suitably resist heat flow. In addition, mineral wool is naturally moisture resistant \cite{mineral_wool}.

\subsection{Glazing Selection}

Glazing refers to the top cover of the solar collector. It has three main purposes:

\medskip
\begin{enumerate}[itemsep=3mm, parsep=-1mm, label=\roman*.]
    \item Protect the internal components from the outside environment.
    \item Minimize heat loss due to convection and radiation from the absorber plate.
    \item Allow as much solar radiation through as possible.
\end{enumerate}

\medskip
The two main materials used for solar collector glazing are glass and polycarbonate.

\medskip
The main parameter that was considered when choosing the glazing is the transmittance. Transmissivity is a measure of how much light passes through the object for a given wavelength. For a solar collector, the glazing should let through as much sunlight as possible but be opaque to the infrared radiation emitted by the absorber plate. This will allow for the most heat gain possible. The secondary parameter, which should be minimized is the reflectance of the glazing. The reflectivity is represents the fraction of reflected solar rays. \cite{emissivity}.

\medskip
Another important factor to consider is the solar heat gain coefficient (SHGC). The SHGC is a measure of how much solar radiation is admitted. A high SHGC rating indicates that the materials are more effective at collecting solar heat, which is better for a solar collector \cite{epri}.

\medskip
\begin{table}[H]
\centering
\caption{Properties of Various Glazing Materials}
\rowcolors{2}{gray!20}{white}
\begin{tabular}{|P{31mm}|P{23mm}|P{23mm}|P{10mm}|P{34mm}|P{17mm}|}
    \hline
    \rowcolor{orangeRed}
    Glazing Type & Temperature Range & Transmissivity & SHGC \cite{glass_glazing}\cite{polycarbonate_glazing} & Thermal Expansion Coefficient $(in/in/F)$ & Density $(kg/m^3)$ \\
    \hline
    Low Iron Tempered Glass \cite{low_iron_glass}  & -50\textdegree C to 240\textdegree C & 91.5\% & $\sim 0.91$ & 4.9E-6  & 2530 \\
    Polycarbonate (Standard) \cite{polycarbonate} & -50\textdegree C to 120\textdegree C & 86\%   & $\sim 0.80$ & 3.75E-5 & 1197 \\
    Sun-Lite \cite{fiberglass}                 & -50\textdegree C to 120\textdegree C & 86\%   & $\sim 0.80$ & 3.6E-5  & 1200 \\
    Lexan 9034 \cite{lexan}               & -40\textdegree C to 100\textdegree C & 88\%   & $\sim 0.80$ & 3.75E-5 & 1197 \\
    SunTuf \cite{suntuf}                   & -40\textdegree C to 100\textdegree C & 90\%   & $\sim 0.80$ & 3.6E-5  & 1200 \\
    \hline
\end{tabular}
\end{table}

\medskip
As seen from Table 4 above, all the materials found met the temperature requirement of -30\textdegree C to 30\textdegree C. Low iron tempered glass was found to have the highest transmissivity, highest solar heat gain coefficient, and lowest coefficient of thermal expansion. Glass was found to be more opaque to the long wave radiation emitted by the absorber plate, and therefore better at trapping heat \cite{low_iron_glass_vs_regular}. Whereas polycarbonate was found to transmit more IR radiation \cite{plexiglass}. Additionally, polycarbonate will yellow over time from exposure to UV rays \cite{polycarbonate_yellowing}; this will reduce the amount of light transmitted by it. However, glass is more than two times heavier than the polycarbonate sheets and more prone to breaking. So extra care will need to be taken when installing it in the collector.

\subsection{Plate Material Selection}

The absorber plate is the component which absorbs solar radiation and emits it as infrared radiation. This heat is then absorbed by the copper piping and then the refrigerant. For this purpose, the plate must have high absorptivity, heat conductivity, and emissivity. The most common materials for the absorber plate are copper, aluminum, and steel; the thermal conductivities of these metals are $398 W/mK$, $247 W/mK$, and $45 W/mK$ respectively \cite{thermally_conductive_materials} \cite{thermal_conductivity_of_steel}. Steel was found to have too low thermal conductivity for this application. The price of copper was \$9.55/kg \cite{copper_prices} and aluminum was \$6.33/kg \cite{aluminum_prices}. Aluminum was selected for our application because it was more readily available.

\medskip
A selective coating was applied to the absorber plate to increase the amount of sunlight absorbed.Thurmalox 250 was identified as a coating specifically suited for solar thermal collector application. The coating possesses a high absorbance and low emissivity, so all the absorbed heat will be transferred to the aluminum plate. It is capable of withstanding high temperatures and is  UV resistant. \cite{high_temp_coating}.

\subsection{Manifold Design}

To determine the copper tube design beneath the absorber plate of the solar flat plate collector, it was convenient to create a two-dimensional drawing to determine the layout. The design of the tubing helped determine the overall length of tubing that would be required. A serpentine tube design was selected as it maximizes the amount of surface area, and for R-134A, for heat transfer to occur within a limited amount of space \cite{serpentine_bending}.

\medskip
The serpentine copper tube design for the flat plate collector was completed based upon the following criteria:

\medskip
\begin{enumerate}[itemsep=3mm, parsep=-1mm, label=\roman*.]
    \item Tube pitch of 3/4 inches [19.05 mm].
    \item Tube bend diameter of 3 15/16” [100 mm].
    \item Leave 1 15/16” [50mm] on each side of absorber plate.
\end{enumerate}

\medskip
In the following figure, two designs were created, (a) and (b). Both designs have an equal manifold spacing. The design for (a) was selected as this design leads to a greater surface area allowing for more heat transfer to occur. With the design for (a) having more U-bends in the tubes, this allows for more time for heat transfer to take place with R-134A. 

\begin{figure}[ht]
    \centering
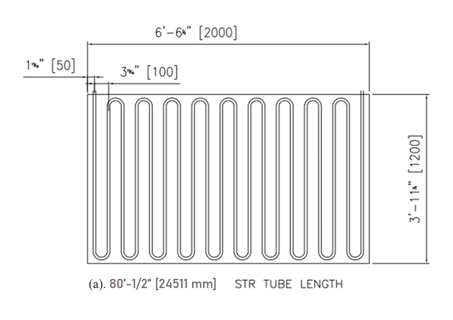
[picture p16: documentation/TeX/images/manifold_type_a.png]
    \subfloat[\centering Horizontally Spaced Manifold] {{}}
    \qquad
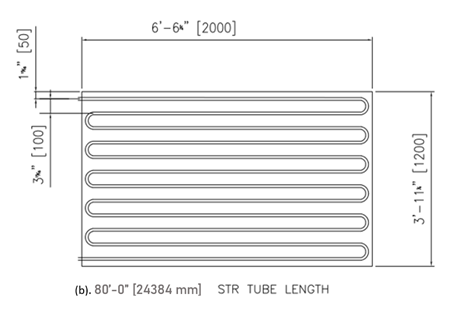
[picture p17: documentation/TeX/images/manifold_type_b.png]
    \subfloat[\centering Vertically Spaced Manifold] {{}}
    \caption{Two-Dimensional Designs of Serpentine Copper Tube Manifold}
\end{figure}

\subsection{Final Collector Model}

\begin{figure}[H]
    \centering
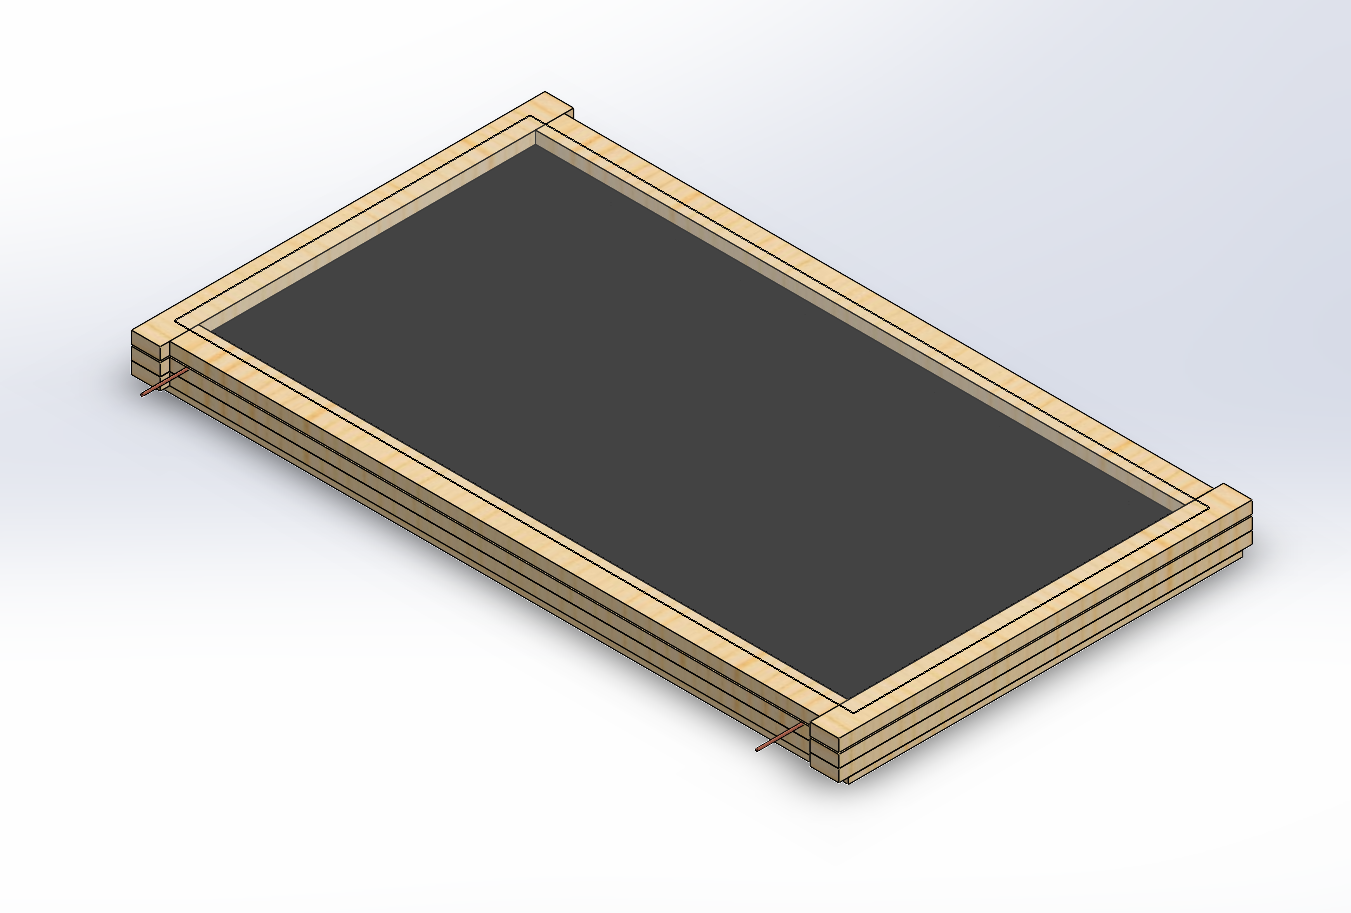
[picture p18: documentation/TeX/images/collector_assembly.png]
    
    \caption{SOLIDWORKS Assembly of Solar Thermal Collector}
\end{figure}

\medskip
Although the collector frame is a simple enclosure, sizing limits and assembly considerations has to be considered. The wood casing was created in multiple parts and grooves were added to account for the thermal expansions of both the glass and absorber plates during winter thermal contractions and summer thermal expansions. 

\medskip
The depth of the grooves were determined using the equation for linear thermal expansion.
\begin{align}
    \Delta L = \alpha_L L_c \Delta T
\end{align}

\medskip
The order in which the components were assembled was taken in consideration to avoid scenarios where components are blocked by other ones. As component selection was finalized, fitment tolerances were added.
\medskip

\section{Component Selection}

For component matching, external to the solar flat plate collector, suitable components and materials for the system based on data and design parameters were selected. The components included the compressor, condenser, expansion valve, control system, and minor parts. The evaluation of manufacturing methods and metal-joining processes, such as, brazing, soldering and/or welding, and use of items such as couplings, and tube adapters were also considered.

\subsection{Compressor Selection}

A compressor is required after the collector to meet the domestic hot water requirements.

\medskip
The compressor selection was based on the lowest evaporating temperature of -6°C. However, the operating envelope of the compressor can reach an evaporation temperature of -8\textdegree C before it automatically shuts down. The fixed speed scroll compressor will allow for the domestic hot water to be heated to 55\textdegree C. The following figure shows the operating envelope of the compressor sponsored by Emerson.

\begin{figure}[H]
    \centering
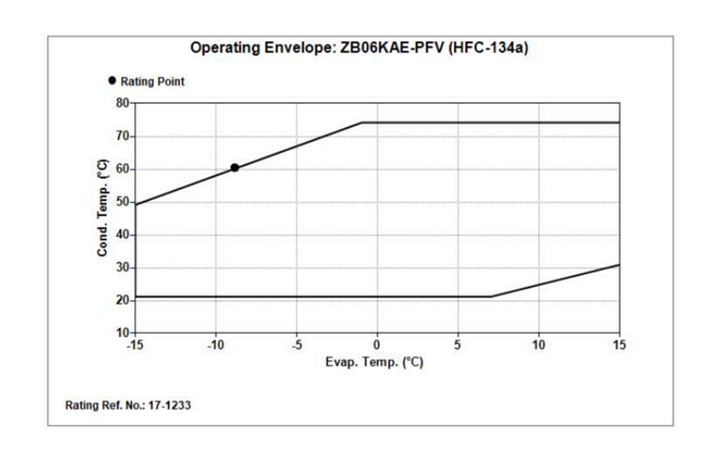
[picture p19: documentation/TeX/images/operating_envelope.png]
    
    \caption{Operating Envelope of the Fixed Speed Scroll Compressor}
\end{figure}

\medskip
The compressor was also evaluated based on the criteria shown below: 

\medskip
\begin{enumerate}[itemsep=3mm, parsep=-1mm, label=\roman*.]
    \item Compatibility with R-134A.
    \item Evaporation Temperature Range: -6\textdegree C to 14\textdegree C.
    \item Compressor Rated Power: 0.75 HP to 1.25 HP.
\end{enumerate}

\medskip
The power requirement for the compressor was found to be 1.138 horsepower based on the required flow rate. The single-phase, 208/230 Volts at 60 Hertz, fixed speed scroll compressor was selected for this project. These types are commonly used for many residential heat pump applications. It may be applied for the purposes of the DX-SAHP as it operates at low capacities, requiring less input power. Compared to its hermetic reciprocating counterparts, the Copeland scroll compressor is simpler to incorporate into new designs and additional design costs \cite{copeland}. The benefits of this type were previously discussed under the HVAC Types in this report.

\medskip
The following figure shows the fixed speed scroll compressor.

\medskip
\begin{figure}[H]
    \centering
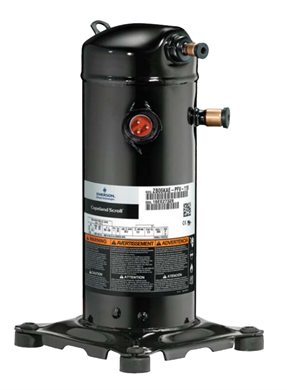
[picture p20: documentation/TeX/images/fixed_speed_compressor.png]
    
    \caption{Fixed Speed Scroll Compressor}
\end{figure}

\medskip
The compatibility between the fixed speed scroll compressor and electronic expansion valve is crucial as this controls the pressure differential of R-134A through the compressor and the amount of flow rate through the valve. The external sponsors of Emerson were provided with the design specifications, controller requirements, and refrigerant parameters to size these components. The copper piping, having a diameter of 3/8 inches, is to be connected to the suction and discharge of the compressor and valve. The determination of the diameters and materials of these lines were communicated with the sponsor as to allow the easiest route for metal-joining and installation purposes. The external piping to the suction/discharge lines of both the compressor and valve, were accomplished by brazing the copper piping to the connecting tubes and additional pipe connections and fittings were used. 

\subsection{Condenser Selection}

A series of condenser designs were considered before settling on the final configuration. However, all the designs had to meet the five basic criteria below:

\medskip
\begin{enumerate}[itemsep=3mm, parsep=-1mm, label=\roman*.]
    \item Maximum condensing coil temperature of 85\textdegree C.
    \item Maximum condensing coil pressure of 3800kPa.
    \item Total possible heat rejection of 2.5kW.
    \item Condensing coil must be compatible with R-134A.
    \item Storage capacity of 225L.
\end{enumerate}

\medskip
The initial idea for the condenser was to use an insulated water tank with an integrated helical copper coil on the inside shown in Figure 3.10 below. However, sourcing these pre-built tanks with the aforementioned criteria was difficult. This condensing unit was broken down into its basic components in the next designs.

\medskip
\begin{figure}[H]
    \centering
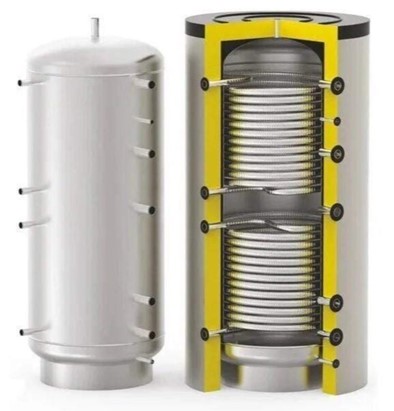
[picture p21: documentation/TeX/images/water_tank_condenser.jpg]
    
    \caption{Water Tank with Two Condensing Coils \cite{water_tank_selection}}
\end{figure}

\medskip
The second design consisted of an insulated water tank with an external heat exchanger as shown in Figure 3.11 below. The water would be pumped from a cold-water storage tank, through the now external heat exchanger, and stored in an insulated tank. The external heat exchanger shown is a coaxial coil condenser. This configuration required the use of a pressure actuated water regulating valve to control the flow rate of water into the coaxial condenser coil. The valve opening is controlled by the pressure in the refrigerant side. This was to allow the water to be heated from 10\textdegree C to 55\textdegree C in a single pass through the coil. There were two main drawbacks to this design. The first being that, since the water is continually being heated from 10\textdegree C to 55\textdegree C, the compressor would constantly be working at its maximum capacity; this in turn would increase the work in $W_in$ and thus reduce the $COP$. Secondly, if the water is not heated to 55\textdegree C in a single pass, there is no process to reuse and reheat this water. This may lead to frequently wasting water during testing as the unheated water would have to be disposed. Therefore, the system was reworked.

\medskip
\begin{figure}[H]
    \centering
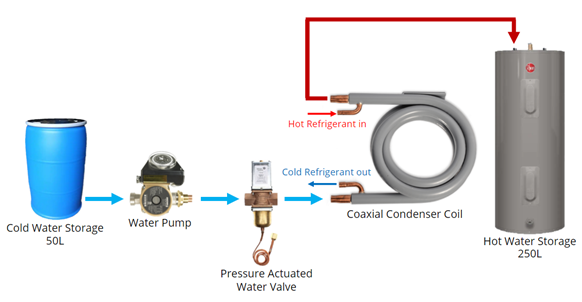
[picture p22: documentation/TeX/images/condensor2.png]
    
    \caption{Second Condensing Design}
\end{figure}

\medskip
The third iteration of the design, shown in Figure 3.12 below, consisted of a water recirculation system to address the previous problems. Additionally, the use of a cold-water storage tank was not required with this design. The main disadvantage of this design is that, as the water heats up, the rate of heat transfer between the refrigerant and water will decrease leading to a lower $COP$. However, as the water temperature difference decreases, the compressor draws less power to heat the preheated water. This means that the overall $COP$ of the system would be higher than if there was no recirculation. Furthermore, since the water is recirculated, the use of a pressure actuated valve is no longer required. The valve may cause a decrease in $COP$ due to the compressor doing more work to heat the water from 10\textdegree C to 55\textdegree C during startup even if sunlight is not available. In a recirculation system without the pressure actuated valve, the water will most efficiently be heated when there is available sunlight and will not have to rely on the compressor during periods of low irradiance.

\medskip
\begin{figure}[H]
    \centering
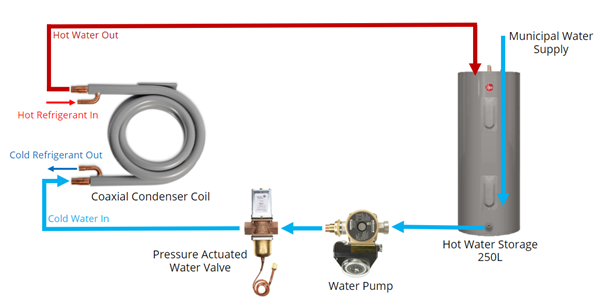
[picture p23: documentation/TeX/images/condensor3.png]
    
    \caption{Third Condensing Design}
\end{figure}

\medskip
This results in the fourth and final design, without the pressure actuated water regulating valve, shown in Figure 3.13 below. The water is recirculated from the hot-water storage tank to the condenser coil and back by the pump.

\medskip
\begin{figure}[H]
    \centering
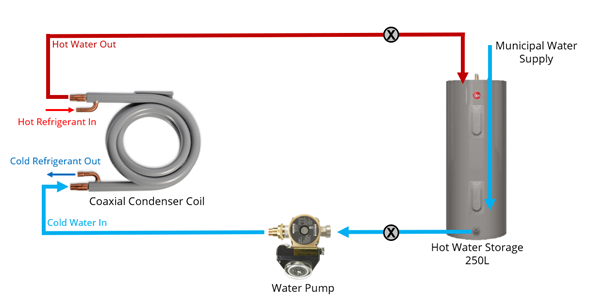
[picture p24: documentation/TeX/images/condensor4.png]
    
    \caption{Fourth (Final) Condensing Design}
\end{figure}

\medskip
For this final design, the components were selected as shown below.

\subsubsection{Condenser Piping}

\medskip
Sharkbite connections with \nicefrac{3}{4}" PEX piping was chosen for ease of assembly. The allowable temperature range was also 0.5\textdegree C to 93.3\textdegree C \cite{pex_tech}, more than enough for this application. 

\subsubsection{Hot-Water Tank}

\medskip
A 250L hot-water tank could not be easily sourced, so for the purpose of testing, a 178L Rheem hot-water tank was chosen \cite{hot_water_tank}. Once the 178L is heated to 55\textdegree C, the water can be dumped to allow for new water to be heated.

\medskip
\begin{figure}[H]
    \centering
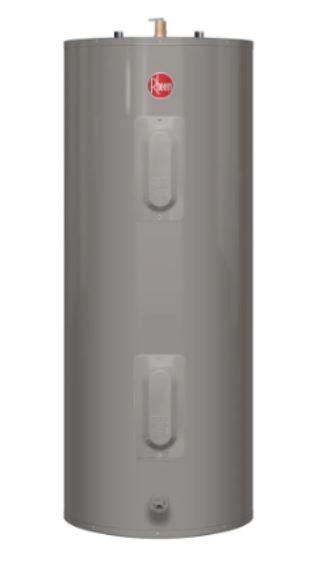
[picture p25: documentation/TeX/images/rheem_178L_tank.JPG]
    
    \caption{Rheem 178L Hot-Water Tank}
\end{figure}

\subsubsection{Condenser Coil}

\medskip
The external heat exchanger is a \nicefrac{3}{4} ton counterflow coaxial coil condenser \cite{coax_coil}.

\medskip
\begin{figure}[H]
    \centering
    
    \caption{\nicefrac{3}{4} ton counter flow coax coil}
\end{figure}

\subsubsection{Water Side Pressure Drop}

\medskip
The pressure drop had to be found to find a suitable water pump. The sources of the drop in pressure are from pipe friction, change in height, pipe bends, and the condenser coil itself. These were calculated for a \nicefrac{3}{4}” pipe as shown below:

The pressure drop due to friction can be found for PEX piping from the tables shown in Figure 3.16 below.

\begin{figure}[H]
    \centering
    
    \caption{PEX Piping Pressure Drop Table}
\end{figure}

\medskip
The required flow rate can be calculated from the following \cite{water_valve}:
\begin{align}
    Flow\ [GPM] = \ddfrac{Tons\ of\ Refrigeration \times 15000}{500\times (T_{out}-T_{in})}
\end{align}

\medskip
This tells us the required flow rate to heat the water from the inlet to the outlet temperature (10 \textdegree C to 55 \textdegree C), in a single pass through the condenser, is 0.5GPM. However, since this design recirculates the water, it is not required to go from 10 \textdegree C to 55 \textdegree C in a single pass. This means that for faster flow rates, the change in water temperature would decrease, and more passes through the condenser are needed. For a flow rate of 1.8GPM, the change in temperature is 12.5 \textdegree C.

\medskip
The pressure drop from a change in height is calculated as \cite{fluid_mechanics}:
\begin{align}
    P_h = \rho g h
\end{align}

\medskip
The change in height will depend on the height of the piping above the hot water tank since it is being recirculated.

\medskip
The pressure drop from the coaxial condenser coil can be found from the manufacture specified table shown in Figure 3.17 below:

\begin{figure}[H]
    \centering
    
    \caption{Coaxial Coil Pressure Drop Table}
\end{figure}

\medskip
Finally, the pressure drop due to bends in the piping can be calculated as \cite{fluid_mechanics}:
\begin{align}
    \Delta P_{elbow} = \ddfrac{K_L\rho w}{2}
\end{align}

\medskip
$K_L$ is the loss coefficient of the specified component or elbow. The loss coefficient for a regular 90\textdegree threaded elbow is 1.5.

\subsubsection{Hot Water Recirculating Pump}

Since the water is recirculating, the pump must meet the minimum required head which was found to be $\sim4.5ft$ for a flow rate of 2GPM making conservative estimates for the length of piping, number of elbows, change in height, and pressure drop from the condenser.

\medskip
The Astro Express 2 hot water pump \cite{astro_express} was selected for this purpose. It can handle temperatures up to 60\textdegree C. The pump curves are shown in Figure 3.18 below.

\begin{figure}[H]
    \centering
    
    \caption{Astro Express 2 hot water recirculating pump}
\end{figure}

\begin{figure}[H]
    \centering
    
    \caption{Astro Express 2 Pump Curves}
\end{figure}

\subsection{Electronic Expansion Valve Selection}

Selection of electronic expansion valves (EXV) was based on the following criteria:

\medskip
\begin{enumerate}[itemsep=3mm, parsep=-1mm, label=\roman*.]
    \item Suitable for HFC refrigerants (i.e., R-134A).
    \item Rated Capacity (kW).
\end{enumerate}

\medskip
Firstly, the selected valve must be compatible with the chosen refrigerant (i.e., R-134A).

\medskip
Secondly, the expansion valve must be able to provide the needed pressure reduction for system parameters. This is usually given by a vendor through an EXV’s capacity rating, which references the system’s heat removal rate in kW. Vendors provide a capacity rating for the following refrigerant conditions, based on AHRI standards \cite{exv_performance}:

\medskip
\begin{table}[H]
\centering
\caption{AHRI Standard Rating Conditions for EXV}
\rowcolors{2}{gray!20}{white}
\begin{tabular}{|P{27mm}|P{35mm}|P{40mm}|P{40mm}|}
    \hline
    \rowcolor{orangeRed}
    Standard Rating Condition & Liquid Temperature at EXV Inlet & Condensing Temperature at EXV Inlet & Evaporating Temperature at EXV Outlet \\
    \hline
    A & 37\textdegree C & 38\textdegree C & 4\textdegree C \\
    \hline
\end{tabular}
\end{table}

\medskip
If the above standard is not used, vendors must specify the operating conditions used instead for their stated rating.

\medskip
Since these operating conditions differ from the ones in the DX-SAHP, a correction factor must be added to the required capacity rating, to compare it with ratings from the vendor. The following information was needed to determine the correction factor:

\medskip
\begin{enumerate}[itemsep=3mm, parsep=-1mm, label=\roman*.]
	\item Refrigerant: R-134A.
	\item Condenser capacity: $Q_L = 2.5 kW$.
	\item Evaporating temperature: $T_{evap} = \SI{-10}{\celsius}$.
	\item Condenser temperature: $T_{cond} = \SI{60}{\celsius}$.
	\item Subcooling: Assume subcooling of $\Delta T_{sub} = 4K$ at inlet of EXV.
\end{enumerate}

\medskip
Based on these conditions, the team received help from Emerson, one of the project sponsors, in selecting the electronic expansion valve. The EX2 3/8X1/2 ODF expansion valve from Emerson was chosen, and Emerson kindly provided the product as well.
\medskip

\subsection{Refrigerant Piping}

Piping is an essential part of a heat pump; it carries the energy gained by the collector and compressor to be released in the condenser. A preliminary analysis was done to determine the drop in pressure between major components in the system. This pressure drop was considered to be from friction in the pipe, elbows, and changes in height. The total pressure drop of the system was necessary in determining the compressor size. The variable definitions for all the equations below can be found in Appendix A.

\medskip
The equation for pressure drop due to friction in a circular pipe is given as \cite{fluid_mechanics}:
\begin{align}
    \Delta P_f = \ddfrac{fL_p \rho w^2}{2D_i}
\end{align}

\medskip
The friction factor, f, was calculated separately for laminar and turbulent flows; however, in this system, only turbulent flows were found. For turbulent flow, the Colebrook White equation \cite{fluid_mechanics} was used to calculate the friction factor. This was solved by moving all terms to one side and using the \verb|fzero| MATLAB \cite{MATLAB} function to iteratively solve for the friction factor.
\begin{align}
    \frac{1}{\sqrt{f}} = -2.0log\left( \ddfrac{\frac{e}{D_i}}{3.7} + \frac{2.51}{Re\sqrt{f}}\right) 
\end{align}

The Reynold’s number determines the type of flow (i.e., Laminar, turbulent, or transitioning). If greater than 2320, the flow was considered turbulent. The Reynold’s Number was calculated as \cite{fluid_mechanics}:
\begin{align}
    Re = \ddfrac{wD_i}{\nu} = \ddfrac{\rho w D_i}{\mu}
\end{align}

\medskip
The values of density and viscosity were found using MATLAB to access CoolProp [18]. By specifying two state parameters, temperature and quality, the density and viscosity were obtained.

\medskip
The velocity of the refrigerant was calculated as:
\begin{align}
    w = \ddfrac{\dot m}{\frac{\rho \pi D_i^2}{4}}
\end{align}

\medskip
The pipe length between sections was assumed to be one meter for these calculations. Therefore, the pressure drop is shown per meter.

\medskip
The pressure drops were found for each section as described below:

\medskip
\begin{enumerate}[itemsep=3mm, parsep=-1mm, label= S\arabic*:]
	\item Between 1 (Compressor) and 2 (Condenser Inlet).
    \item Between 2 (Condenser Exit) and 3 (Expansion Valve).
    \item Between 3 (Expansion valve) and 4 (Evaporator Inlet).
    \item Between 4 (Evaporator Exit) and 1 (Compressor).
\end{enumerate}

\begin{figure}[H]
    \centering
    
    \caption{Pressure Drop for \nicefrac{1}{4}, \nicefrac{5}{16}, \nicefrac{3}{8}, \nicefrac{1}{2}, \nicefrac{3}{4}, and 1 inch Diameter Piping at each Section}
\end{figure}

\medskip
As seen from Figures 3.10 \& 3.11 above, as the diameter of the piping decreased, the pressure drop per meter increased drastically. Based on these values however, the pressure drop due to friction for diameters greater than \nicefrac{1}{4}” is insignificant considering the system operating pressures that range from $750kPa$ to $3800kPa$. Additionally, the piping for these sections are all less than a meter.

\medskip
The pressure drop due to elbows was calculated as follows \cite{fluid_mechanics}:
\begin{align}
    \Delta P_e = \ddfrac{K_L \rho w^2}{2}
\end{align}

\medskip
$K_L$ is the loss coefficient of the specified component or elbow. The loss coefficient for a long radius 90\textdegree \ flanged elbow is 0.2 and the loss coefficient for a regular 90\textdegree \ threaded elbow is 1.5 \cite{fluid_mechanics}.

\medskip
The pressure drop due to a change in height was calculated as \cite{fluid_mechanics}:
\begin{align}
    \Delta P = \rho g \Delta z
\end{align}

\medskip
The pressure drop due to elbows are shown for one elbow for each section below.

\medskip
\begin{figure}[H]
    \centering
    
    \caption{Pressure Drop from a Long Radius 90\textdegree \ Elbow vs. a Threaded 90\textdegree \ Elbow for a \nicefrac{1}{4} inch Pipe}
\end{figure}
\begin{figure}[H]
    \centering
    
    \caption{Pressure Drop from a Long Radius 90\textdegree \ Elbow vs. a Threaded 90\textdegree \ Elbow for a \nicefrac{5}{16} inch Pipe}
\end{figure}
\begin{figure}[H]
    \centering
    
    \caption{Pressure Drop from a Long Radius 90\textdegree \ Elbow vs. a Threaded 90\textdegree \ Elbow for a \nicefrac{3}{8} inch Pipe}
\end{figure}
\begin{figure}[H]
    \centering
    
    \caption{Pressure Drop from a Long Radius 90\textdegree \ Elbow vs. a Threaded 90\textdegree \ Elbow for a \nicefrac{1}{2} inch Pipe}
\end{figure}
\begin{figure}[H]
    \centering
    
    \caption{Pressure Drop from a Long Radius 90\textdegree \ Elbow vs. a Threaded 90\textdegree \ Elbow for a \nicefrac{3}{4} inch Pipe}
\end{figure}
\begin{figure}[H]
    \centering
    
    \caption{Pressure Drop from a Long Radius 90\textdegree \ Elbow vs. a Threaded 90\textdegree \ Elbow for a 1 inch Pipe}
\end{figure}

\medskip
As seen from Figures 3.20 - 3.26 above, the drop in pressure follows the same trend when decreasing the pipe diameter; smaller diameter has larger pressure drops. Additionally, the threaded 90\textdegree \ elbow yields more drop in pressure than the pipe with a large radius elbow as expected.

\medskip
When considering the operating point of the entire system from $750kPa$ – $3800kPa$, the pressure drops due to the piping is insignificant. The currently built refrigerant side piping uses \nicefrac{5}{16} and \nicefrac{3}{8} inch pipes. The maximum pressure drop was found to occur between 3 (Expansion valve) and 4 (Evaporator Inlet). The piping length between these sections in the design is less than 0.5m. In this section, the maximum pressure drop from friction for \nicefrac{5}{16} inch piping was found to be $46.5kPa$ per meter. The maximum pressure drop from elbows for \nicefrac{5}{16} was found to be $36.6kPa$ per elbow. The maximum pressure drop from friction for \nicefrac{3}{8} inch piping was found to be $18.6kPa$ per meter. The maximum pressure drop from elbows for \nicefrac{3}{8} was found to be $17.7kPa$ per elbow. Due to the compact system design, the pressure drop due to piping can be considered to be negligible.

\subsection{Accessory Parts}

\subsubsection{Receiver}

A receiver was added as per recommendations from Emerson and the HVAC contractor from Chinook Refrigeration. The receiver goes after the condensing unit and before the electronic expansion valve. It stores any excess refrigerant that is not being circulated around the system. Since the DX-SAHP system will be operating through a wide range of ambient conditions, there will be several mass flow rates implemented, and thus a need exists for a method to store the excess refrigerant. Having the receiver ensures space in the system to store the excess refrigerant - preventing it from pooling elsewhere.

\medskip
\begin{figure}[H]
    \centering
    
    \caption{Refrigeration Research 3 lb. Receiver}
\end{figure}

\medskip
A Refrigeration Research 3 lb 1/4" SAE X 1/4" SAE Vertical Receiver \cite{receiver} was selected due to its availability for easy pick-up in Calgary, and an adequate refrigerant storing capacity of 3 lbs. This capacity was chosen with recommendations from the team’s contact at Emerson. 

\subsubsection{Filter Drier}

To keep the system working at optimal conditions, it is necessary to ensure that there are as little contaminants as possible. The potential contaminants in this system are water, copper shavings, or other contaminants during installation. The filter drier ensures these contaminants are not circulated throughout the system and causing damage; it is installed in the liquid-line of the heat pump before the sight glass \cite{sight_glass}.

\medskip
\begin{figure}[H]
    \centering
    
    \caption{EK083S Filter Drier \cite{filter_drier}}
\end{figure}

\subsubsection{Sight Glass}

The sight glass is needed to view the level of the refrigerant to ensure proper operation. If there are bubbles seen through the sight glass it indicates that there is not enough refrigerant in the system. Additionally, the refrigerant must be subcooled before entering the EXV; therefore, the sight glass is installed before the EXV to ensure only liquid enters it \cite{sight_glass_install}.

\medskip
\begin{figure}[H]
    \centering
    
    \caption{\nicefrac{3}{8}" ODF HMI-1TT3 Hermetic Sight Glass Moisture Indicator \cite{liquid_sight_glass}}
\end{figure}

\section{Control System}

The philosophy of having a control system for this design lies in the fact that the heat pump needs to adapt to varying ambient conditions to still meet the desired heat load. For instance, when there is less available sunlight, the refrigerant mass flow rate must be lowered, so the refrigerant can spend an adequate amount of time in the solar thermal collector and fully evaporate.

\subsection{Mass Flow Rate Control}

The mass flow rate of the refrigerant is an important control parameter and dictates how fast the refrigerant is flowing through the system. It is critical that the refrigerant enters the compressor as at least a saturated vapor, as any liquid-vapor mixture will damage the compressor. The refrigerant must spend enough time in the solar collector to ensure full phase-change is achieved. The time spent in the collector is directly linked to mass flow rate and thus it is critical that this parameter be controlled. For example, during colder conditions where there is less available sunlight, the system needs to be able to lower the flow rate so that the refrigerant can spend more time in the collector to completely changing phase.

\medskip
Mass flow rate will be controlled by the electronic expansion valve. There is a stepper motor in the valve that incrementally opens and closes the valve opening, to adjust the flow rate. This stepper motor responds to electronic signals that will be fed by an external controller. The Emerson super heat controller (Model: XEV12D) was selected as it is compatible with the system’s chosen electronic expansion valve. This superheat controller was generously provided by the team’s industry sponsor, Emerson. The controller input parameters include the refrigerant type, and the solar collector exit temperature and pressure. The temperature and pressure measurements will be given by an 20J NTC thermistor temperature sensor and an 20J NTC pressure transmitter, which are recommended from the controller’s operator’s manual, and were also supplied by Emerson. The controller must optimize the mass flow rate to ensure that the refrigerant is at least a saturated vapor as it exits the collector, while still reducing the amount of superheat if possible. This is because excessive superheating at the outlet of the collector is an indicator that there is not enough refrigerant passing through and the mass flow rate should be increased. If the mass flow rate is needlessly low, the collector plate average temperature will increase, and $COP$ of the system will fall.

\begin{figure}[H]
    \centering
    
    \caption{EXV Controller with Compatible Temperature and Pressure Sensors}
\end{figure}

\medskip
The wiring of the superheat controller will be done by Chinook Refrigeration.

\subsection{Water Pump Control}

The mass flow rate of the water is decided based on the condensing temperature selected and the coaxial condensing coil’s data sheet. In order to integrate the water circulation with the rest of the heat pump controls, a contactor is used. The contactor is used to turn the compressor on and off and is wired to it externally. Using an auxiliary switch that can be connected to the three-pole contactor, it is possible to turn the water pump on and off in tandem with the compressor. This allows both the refrigerant side and water side of the DX-SAHP to be turned on and off simultaneously. The wiring of the contactor will be done by Chinook Refrigeration.

\begin{figure}[H]
    \centering
    
    \caption{Three-pole Contactor (right) and Auxiliary Switch (left)}
\end{figure}

\medskip
Currently an automatic shut down of the system is missing. In future iterations, an additional control element that turns off the full system once the water in the tank is homogeneously at 55 \textdegree C can be integrated.

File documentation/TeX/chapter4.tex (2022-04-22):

\chapter{Prototyping and Testing}

\section{Simulation Results}

As previously discussed, the developed MATLAB model featured a winter and summer scenario to estimate the theoretical performance of the DX-SAHP system. The results of the simulation indicate that the system would be capable of provisioning 1.1 KWh of power with an average $COP$ of 2.4 for the winter scenario. During the summer months, when irradiance levels are higher, and ambient temperatures are warmer, the system would be able to generate 2 KWh of power with an average $COP$ of 3.0, virtually satisfying the entirety of the hot water heat load demand ($\sim2KW$). The collector efficiency was also determined to range between 51\% to 74\%, which is comparable to the efficiency of locally manufactured flat plate solar thermal collectors. The figure below depicts the performance of the DX-SAHP system during a harsh winter day with low irradiance levels, confirming the feasibility of the system for cold climates. 

\medskip
\begin{figure}[H]
    \centering
    
    \caption{Simulation Results for an Average Winter Day}
\end{figure}

\section{Developed Prototype}
\subsection{Refrigeration Assembly}
\subsubsection{Aluminum Absorber Plate to Copper Manifold Bonding}

The bonding of the copper tubing to the aluminum plate was necessary as to minimize any air gaps present that would affect the thermal performance of the system. The method of bonding was evaluated based on the following options:

\medskip
\begin{enumerate}[itemsep=3mm, parsep=-1mm, label=\roman*.]
    \item Brazing or Soldering.
    \item Thermally Conductive Epoxy Adhesive.
    \item Copper Strapping with Threaded Steel Galvanized Screws.
\end{enumerate}

\medskip
Due to the dissimilar thermal properties of the two metals, brazing copper to aluminum is not a suitable option. The appropriate brazing technology and flux must be used for this process to be applicable. The issues with brazing copper to aluminum is mainly due to aluminum having a much lower melting point than copper. The melting points of aluminum and copper are respectively, approximately $650$ \textdegree C and over $1000$ \textdegree C. The flame is typically directed on the copper and as heat transfers from the copper to the aluminum, the copper tends to melt quicker while copper is still absorbing the heat. This process accelerates the destruction of the aluminum components \cite{brazingALCU} and results in an insufficient bond.

\medskip
For additional expertise, the team contacted several companies including those who deal with specialized welding. The option of brazing or soldering the two dissimilar metals was advised against.

\medskip
The second option of thermally conductive epoxy adhesives was then considered. Mainly, epoxy adhesives are used for leaks or refrigeration repairs and thorough research was applied into determining the type of product to use for this application. The investigation into selecting a thermally conductive epoxy adhesive was based on the highest thermal conductivity to later achieve better thermal performance of the system, substrate compatibility, room temperature curing, and having a strong bond. The viscosity of the product to be considered was to be of paste form.

\medskip
A thermally conductive silver epoxy  adhesive was evaluated. This two-part product consisted of a one-hour work time, room temperature curing for 24 hours, and was within a temperature range suitable for the system. This product was an excellent choice for aluminum and copper as well as having a thermal conductivity value of $500 W/m^2K$. This product did not work for bonding the copper tubing to the aluminum plate.

\medskip
The team then evaluated the option of securing the copper tubing to the aluminum plate by use of copper strap. The copper strapping was snipped into tiny, flexible brackets which were then drilled into the aluminum plate by use of threaded steel galvanized screws. The screws extending outwards on the opposite end of the plate were then grind and polished.

\medskip
A thermal mastic heat transfer compound was evaluated as the final selection into minimizing the air gaps that were still present due to the copper tubing not being flush with the aluminum plate. The thermal conductivity of this product was not as high as the silver epoxy, however, was quite higher than air and this is mainly what was required. This paste compound did not require curing, does not harden, and does not lose adhesion. This product was applied throughout the entire length of tubing to minimize the air gaps.

\medskip
The following table shows the specifications of the two heat transfer compounds.

\medskip
\begin{table}[H]
\centering
\caption{Specifications - Heat Transfer Compounds}
\rowcolors{2}{gray!20}{white}
\begin{tabular}{|P{60mm}|P{45mm}|P{45mm}|}
    \hline
    \rowcolor{orangeRed}
     & Silver Epoxy Adhesive & Thermal Mastic Compound \\
    \hline
    \textbf{Cure Schedule} & 24h at Room Temperature & N/A \\
    \textbf{Operating Temperature $\SI{}{\celsius}$} & -50 to +170 & -45 to +100 \\
    \textbf{Viscosity} & Paste & Paste \\
    \textbf{Thermal Conductivity $[W/m^2 K]$} & $\sim500$+ & $\sim37$ \\
    \hline
\end{tabular}
\end{table}

\medskip
The following figure shows the final bonding of the copper tubing to the aluminum plate.

\medskip
\begin{figure}[H]
    \centering
    
    \caption{Bonding - Copper Tubing to Aluminum Plate}
\end{figure}

\subsubsection{Casing}

The casing of the collector frame was made with 2x4 lumber and a plywood pine board. The casing was built following the engineering drawing created for assembly - where the finalized rectangular dimensions were: $2.2m \times 1.3m$. With these dimensions, a SOLIDWORKS strain analysis was conducted to determine the maximum deflection of the 5052 H2 aluminum plate sitting on top of the frame. Knowing the weight of the aluminum plate (29.48kg) and the weight of the copper manifold (1.61kg), a point load was applied at the center to determine the maximum deflection of the plate and in turn determine if the dimensions of the casing were still suitable. Although at first glance, the casing is simply a rectangular enclosure, creating the casing was much more difficult than was expected. First the wood was treated with a stain and sealer to prevent rotting in the outside conditions. As the casing was created in a garage without access to proper shop tools such as a planar, the process of creating the casing was much more difficult due to the warped raw lumber. This was counteracted with the use of multiple clamps and PL Premium wood glue.

\begin{figure}[ht]
    \centering
    \subfloat[\centering Collector Engineering Drawing] {{}}
    \qquad
    \subfloat[\centering Collector Wood Casing] {{}}
    \caption{Solar Thermal Collector Design and Fabrication}
\end{figure}

\subsubsection{Frame}

With the Solar Thermal Collector fully assembled, the final weight was determined by simply adding up the combined weights of all components in the collector:

\medskip
\begin{table}[H]
\centering
\caption{Solar Thermal Collector Weights}
\rowcolors{2}{gray!20}{white}
\begin{tabular}{|P{75mm}|P{75mm}|}
    \hline
    \rowcolor{orangeRed}
    Component & Weight $(kg)$ \\
    \hline
    Wood Casing & 61.49 \\
    Absorber Plate Manifold & 31.09  \\
    Glass Glazing & 17.53 \\
    \textbf{Total Combined Weight} & \textbf{110.11kg} \\
    \hline
\end{tabular}
\end{table}

\medskip
Knowing the weight and dimensions of the solar thermal collector, the frame could now be designed. The team first sent these requirements to an external vendor to help create the frame, but was quoted for \$5600. Due to the high price tag of the frame, it was decided that with the help of the Schulich School of Engineering's Makerspace Machine Shop, a frame would be designed and welded in house.

\medskip
The primary failure mode in the frame to be concerned on is column buckling due to the heavy load of the solar collector. To determine the sizing of the steel tubes, the Euler Buckling Equation was utilized with an effective length of 0.25 as a fixed/free end system:
\begin{align}
    F_cr = \ddfrac{\pi ^2 EA}{(\ddfrac{k_{eff}L}{r})^2}
\end{align}
\medskip

Applying the weights on the steel frame distributed evenly across the 4 columns from the preliminary design of the frame as the critical loads, the critical cross sectional area of the tubing was able to be determined. To allow for ease of assembly, and to be conservative in the calculations, it was determined that 1.5" tubing would be more than sufficient in preventing the frame from failing.

\medskip
Knowing the sizing of the steel tubing required, the frame was modelled with 3 key factors in mind:

\medskip
\begin{enumerate}[itemsep=3mm, parsep=-1mm, label=\roman*.]
    \item Easy to disassemble.
    \item Easy to move.
    \item Able to change tilt angle between 45\textdegree and 51\textdegree.
\end{enumerate}

With these criteria, the following frame was designed:

\begin{figure}[H]
    \centering
    
    \caption{Assembly Frame Engineering Drawing}
\end{figure}

\medskip
The assembly was designed in 3 frames with telescoping joints to easily take apart and put back together. Using caster wheels rated for over 1300lbs attached to a steel plate, the system was easily movable. However, the final challenge came in designing the pivot joints to allow for varying tilt angles. Because the solar collector had a piping manifold with refrigerant running through it and was brazed to the other system components, tilting the collector with the frame, would mean the entire system would tilt as well. This is not possible as the other major components of the system were fixed onto the steel base plate.

\medskip
Using the engineering drawings, and cutting the tubing accordingly, the frame was MIG (metal inert gas) welded together. To prevent rusting due to the outside conditions, the frame was also spray painted. With the frame completed, the solar collector was then lifted and placed onto the support members of the frame as seen below.

\begin{figure}[H]
    \centering
    
    \caption{Assembly Frame}
\end{figure}

\subsubsection{Heat Pump Assembly}

External sponsorship was provided by Emerson, supplying the team with many refrigeration components and assistance such as:

\medskip
\begin{enumerate}[itemsep=3mm, parsep=-1mm, label=\roman*.]
    \item Fixed Speed Scroll Compressor.
    \item Pulse Width Modulation Electronic Expansion Valve.
    \item Superheat Controller.
    \item Labour required for piping and the assembly of the refrigeration cycle,.
    \item Leak and pressure testing.
    \item Evacuation/Charging and commissioning of the refrigerant, R-134a.
\end{enumerate}

\medskip
The following figure shows the heat pump assembly for the refrigeration cycle of the DX-SAHP. In the figures below, the heat pump cycle is comprised of four major components – the solar thermal collector, fixed speed scroll compressor, coaxial coil, and the electronic expansion valve. The assembly of the refrigeration cycle consists of the piping that is connected from the outlet of the solar thermal collector to the compressor. The piping to and from the compressor is connected to valves allowing for the compressor to be disassembled in case of any maintenance issues. The piping then leads to the coaxial coil in which the refrigerant exchanges heat with the water. Further, the piping is connected to auxiliary components such as, the receiver, filter drier, and sight glass. Lastly, the piping connects to the electronic expansion valve for the cooled refrigerant to become depressurized. This piping is then connected to the outlet of the solar collector via the copper serpentine manifold attached beneath the aluminum absorber plate. The piping was attached by auxiliary piping connections (i.e., couplings) and fittings as well as brazing.

\medskip
\begin{figure}[H]
    \centering
    
    \caption{Heat Pump Assembly for the DX-SAHP}
\end{figure}

Figure 4.7 shows the final heat pump assembly of the DX-SAHP connected to the piping in the solar thermal collector.

\medskip
\begin{figure}[H]
    \centering
    
    \caption{Full Assembly for the DX-SAHP}
\end{figure}

\subsection{Water Circulation Assembly}

Due to uncertainties with the refrigerant side piping, the layout of the water side was to be determined after. Estimates on the pipe lengths were made to do preliminary calculations. Once the refrigeration side is finalized, measurements will be taken to determined exact pipe lengths and components (i.e., elbows and couplings) required. The piping assembly will be completed using Sharkbite connections which are easy to assemble as they are push-to-fit. Since PEX piping will expand and contract with changes in temperature, care will be taken during installation to ensure there is adequate room to allow for this change in length (1” to 2.5” every 100’).

Once the water side piping is complete, testing can begin.

\subsection{Data Acquisition System}
\subsubsection{Design Validation Goals}

To verify the design and determine the system performance, a data acquisition system was developed. The COP of the DX-SAHP can be defined as,

\begin{align}
    COP = \ddfrac{Q_{out}}{W_{cycle}} = \ddfrac{\dot m (h_2 - h_3)}{\dot m (h_2 - h_1)} = \ddfrac{(h_2 - h_3)}{(h_2 - h_1)}
\end{align}

\medskip
As evidenced by Equation 4.1, the $COP$ of the system can be determined knowing the specific enthalpy of the refrigerant at certain points. Specific enthalpy at any location can be found through use of temperature and pressure measurements and the refrigeration table of R-134A [18]. As so, temperature sensors at 3 locations (1, 2, 3) and pressure sensors at 2 locations (1, 2) on Figure 4.1 below will be used to determine $COP$. The pressure sensor at 3 can be neglected under the isobaric condensation assumption. However, a temperature sensor at 3 is still necessary as it is pertinent to know and minimize the degree of sub-cooling at the inlet of the electronic expansion valve. Additionally, pressure transducers are approximately at least 20 times more expensive than a thermistor at any given location, so the isobaric assumption was also used for economic reasons.

\medskip
In the above $COP$ equation, it was assumed that all the power input into the compressor is going into superheating the refrigerant. This in fact is not valid, as the compressor itself will hold an efficiency factor. This efficiency factor dictates how much power the compressor puts into the refrigerant, from the total power it uses. To evaluate this efficiency factor, the following equation will also be used to determine $COP$,
\begin{align}
    COP = \ddfrac{Q_{out}}{W_{cycle}} = \ddfrac{\dot m_{water}C_p(T_{water, out}-T_{water, in})}{W_{cycle}}
\end{align}
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

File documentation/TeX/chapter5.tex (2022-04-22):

\chapter{Project Management}

\section{Roles and Responsibilities of Team Members}

Each team member played a vital role in the group:

\medskip
\begin{itemize}[itemsep=3mm, parsep=-1mm]
    \item Kerwin oversaw the Project Management of the group and ensured that everything is going according to plan. He also assisted in contacting vendors and setting schedules up. 
    \item Nadia was responsible for the solar collector design and sizing. She was in charge of ensuring that the collector is functional.
    \item Jessica oversaw component matching and contacting sponsors about the component matching. 
    \item Charuka was the assembly lead. He was present during all assembly steps and oversaw much of the frame design as well.
    \item Dhruvi was in charge of the control and data acquisition system. 
    \item Edwin was the testing lead and also oversaw the condenser design.
\end{itemize}
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

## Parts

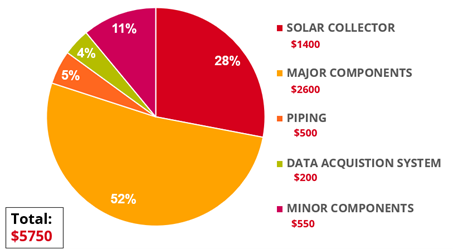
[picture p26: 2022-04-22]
documentation/TeX/images/cost_breakdown.png

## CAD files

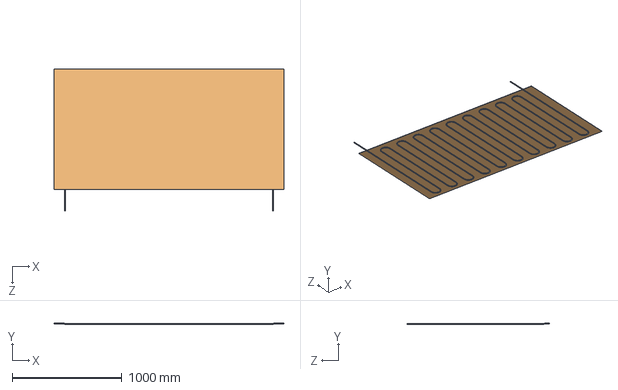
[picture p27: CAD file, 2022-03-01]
model/solar collecter/absorber_plate.SLDASM
2100.0 x 11.1 x 1300.0 mm
serpentine_manifold
absorber

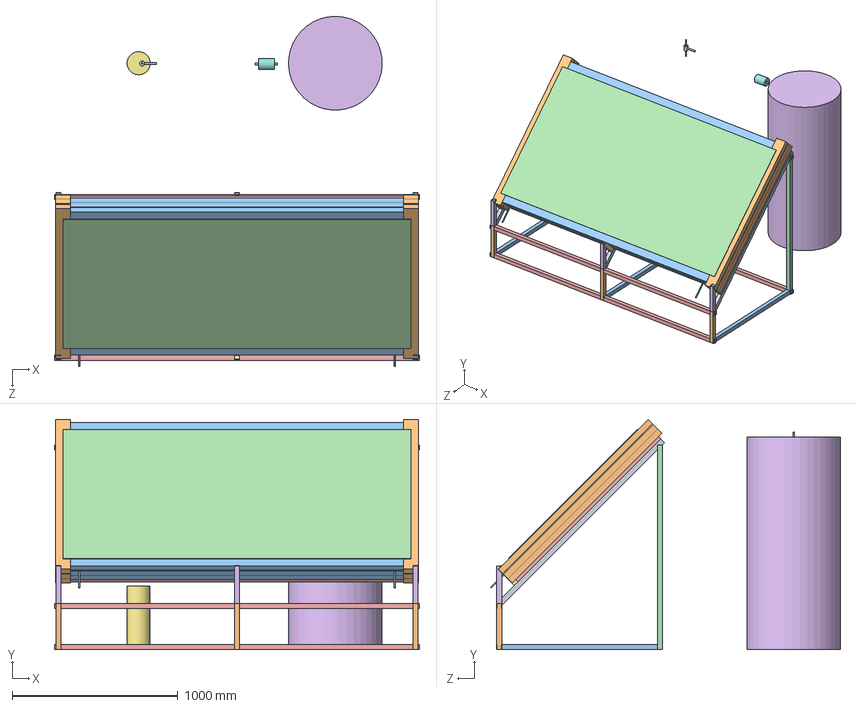
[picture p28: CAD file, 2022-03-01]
model/assembly/final_assembly.SLDASM
2200.0 x 1388.9 x 2111.3 mm
1.25in_square_tubing_1.4m x 3
1.25in_square_tubing_.3m x 3
1.25in_square_tubing_1m x 3
1.25in_square_tubing_1.3m x 3
1.25in_square_tubing_2.2m x 4
1.25in_square_tubing_.1m x 3
1.25in_square_tubing_.15m x 3
serpentine_manifold
absorber
2x4in_width x 6
2x4in_length x 6
glass
4x8ft_plywood_board
hot_water_tank
compressor
filter_drier
exv

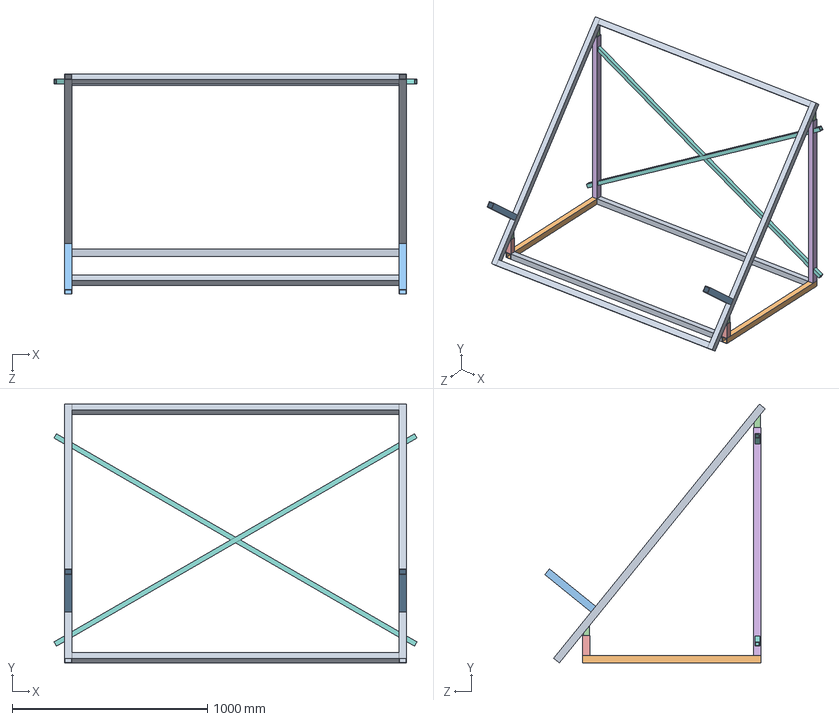
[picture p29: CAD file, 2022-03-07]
model/frame/collector_frame.SLDASM
1860.5 x 1326.8 x 1129.7 mm
1.5in_square_tube_5.5ft x 6
1.5in_square_tube_3ftt x 2
1.5in_square_tube_1ft x 2
1.25in_square_tube_0.50ft_cut x 4
1.5in_square_tube_4in x 2
1.5in_square_tube_46in x 2
1.25in_square_tube_1ft x 2
1in_support_bracing_8ft x 2

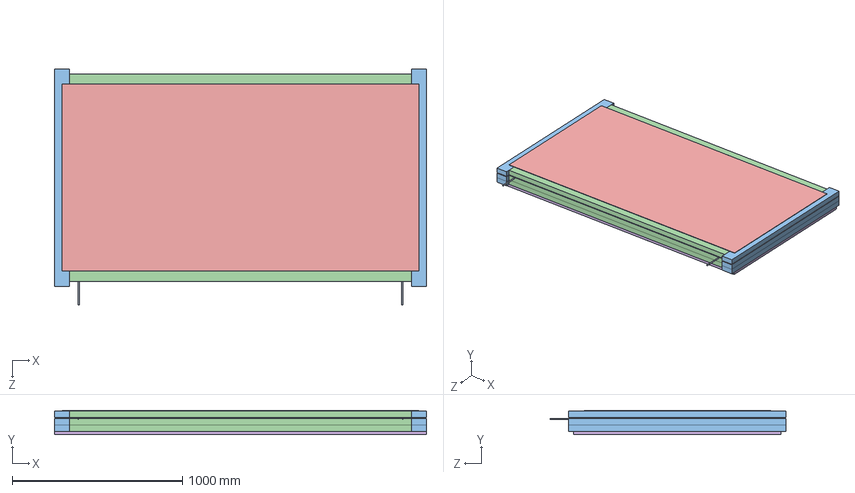
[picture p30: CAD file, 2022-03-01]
model/solar collecter/solar_collector.SLDASM
2185.7 x 141.1 x 1388.9 mm
serpentine_manifold
absorber
2x4in_width x 6
2x4in_length x 6
glass
4x8ft_plywood_board

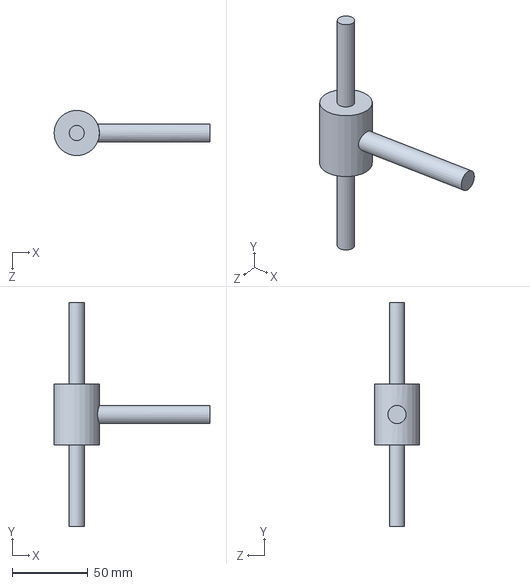
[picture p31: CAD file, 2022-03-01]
model/assembly/exv.SLDPRT
103.0 x 148.0 x 29.8 mm

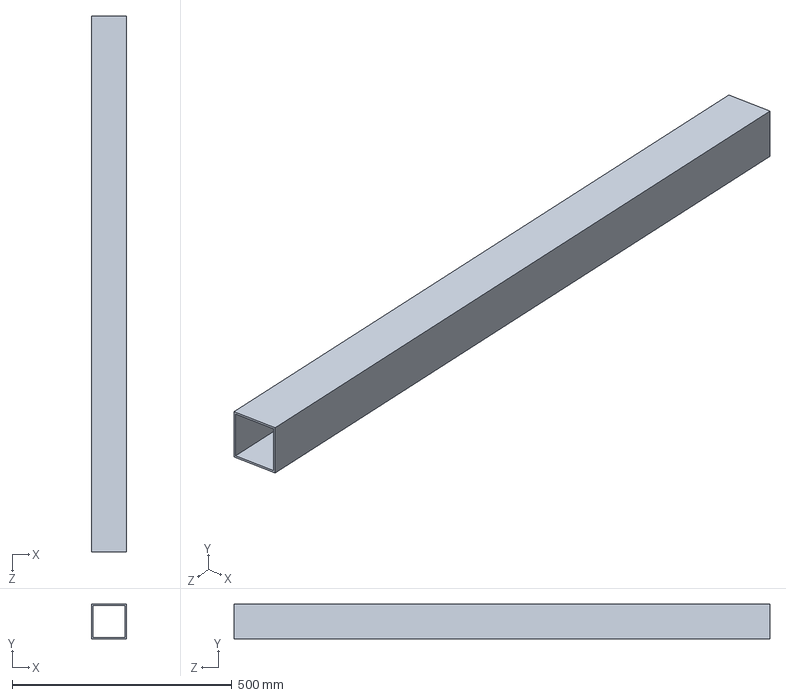
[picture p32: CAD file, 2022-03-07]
model/frame/1in_support_bracing_8ft.SLDPRT
79.2 x 79.2 x 1219.2 mm

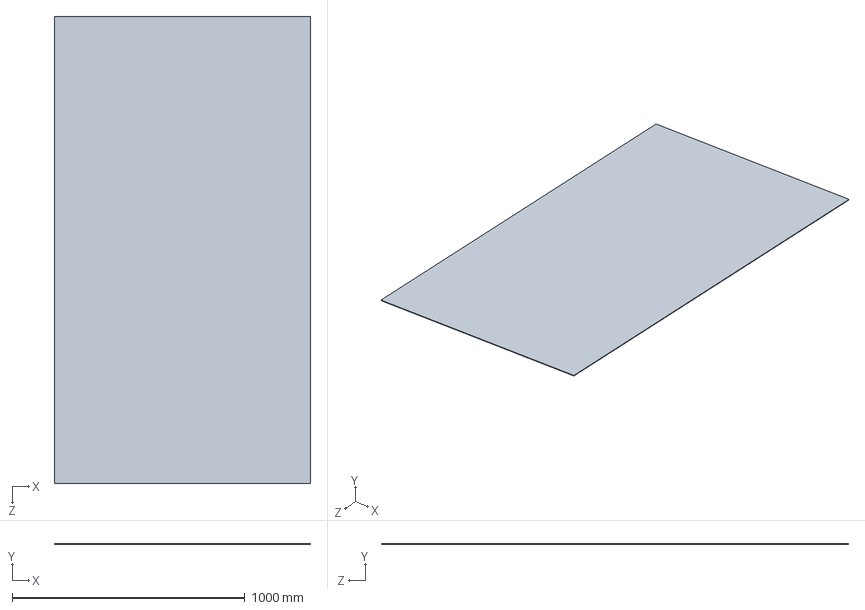
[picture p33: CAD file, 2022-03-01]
model/solar collecter/glass.SLDPRT
1100.0 x 3.00 x 2007.9 mm

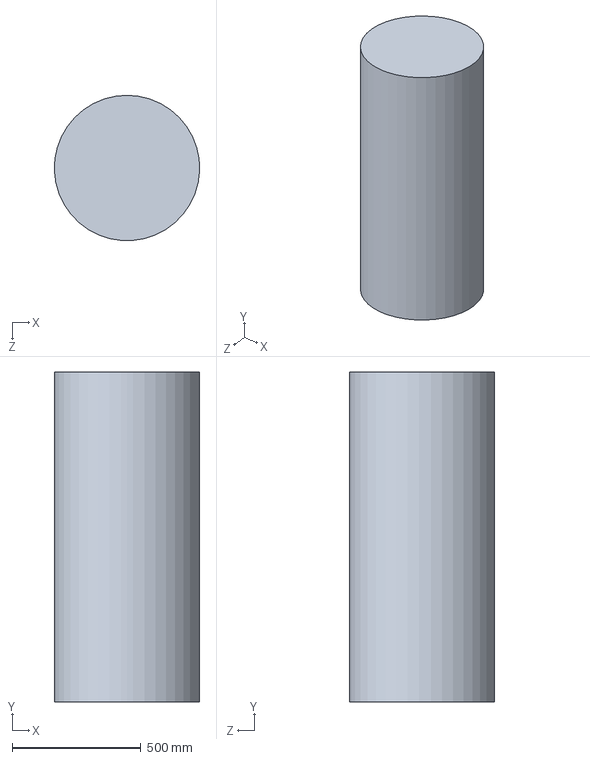
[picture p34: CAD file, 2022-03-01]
model/assembly/hot_water_tank.SLDPRT
564.7 x 1282.7 x 565.2 mm

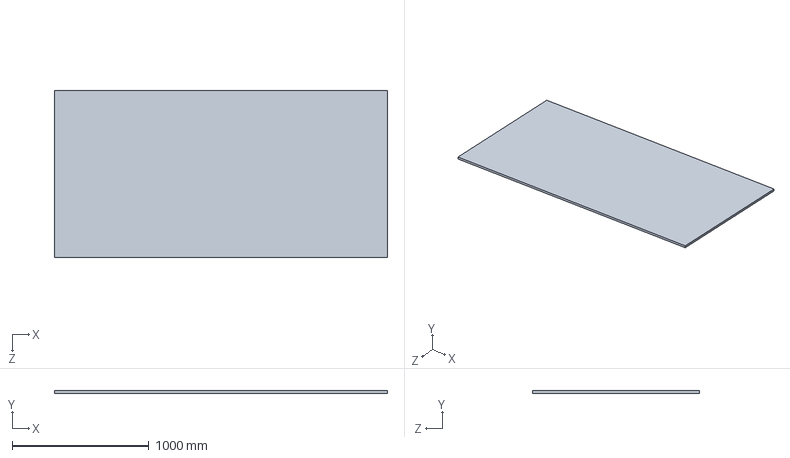
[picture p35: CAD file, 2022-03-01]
model/solar collecter/4x8ft_plywood_board.SLDPRT
2438.4 x 19.1 x 1219.2 mm

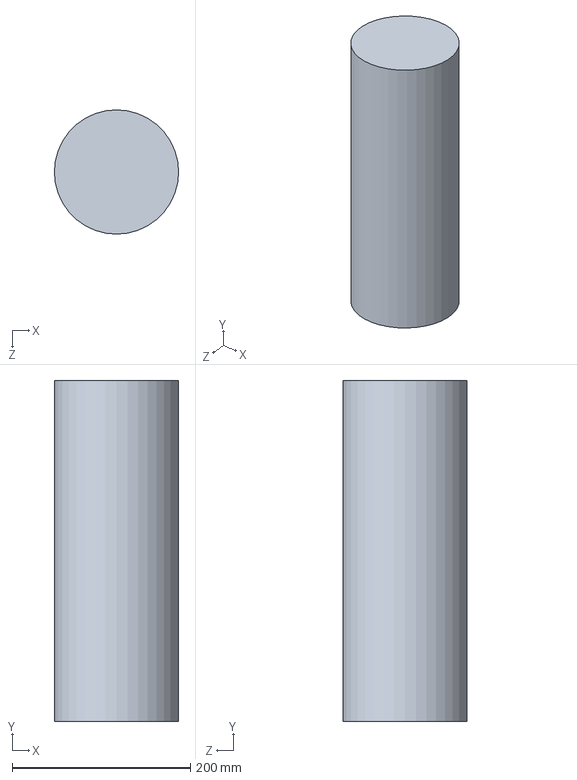
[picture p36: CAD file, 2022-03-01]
model/assembly/compressor.SLDPRT
139.4 x 382.5 x 139.4 mm

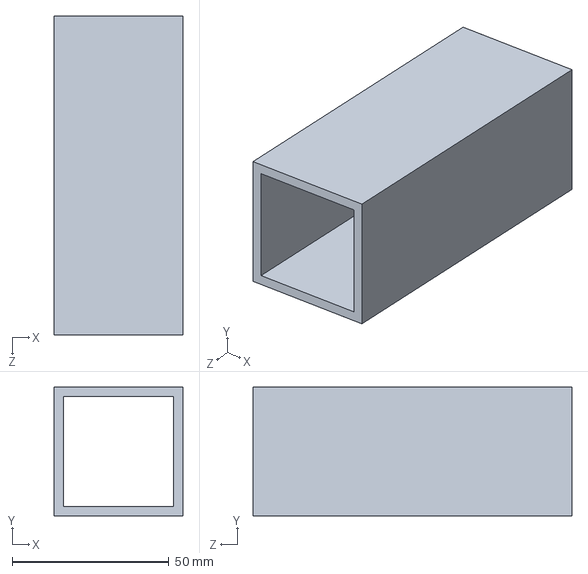
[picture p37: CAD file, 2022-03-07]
model/frame/1.5in_square_tube_46in.SLDPRT
41.1 x 41.1 x 101.6 mm

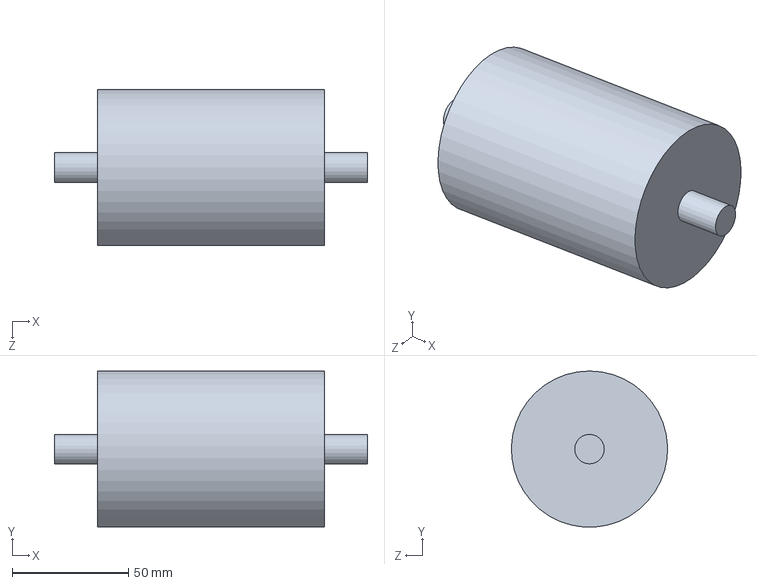
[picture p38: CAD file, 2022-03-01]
model/assembly/filter_drier.SLDPRT
134.4 x 67.0 x 67.0 mm

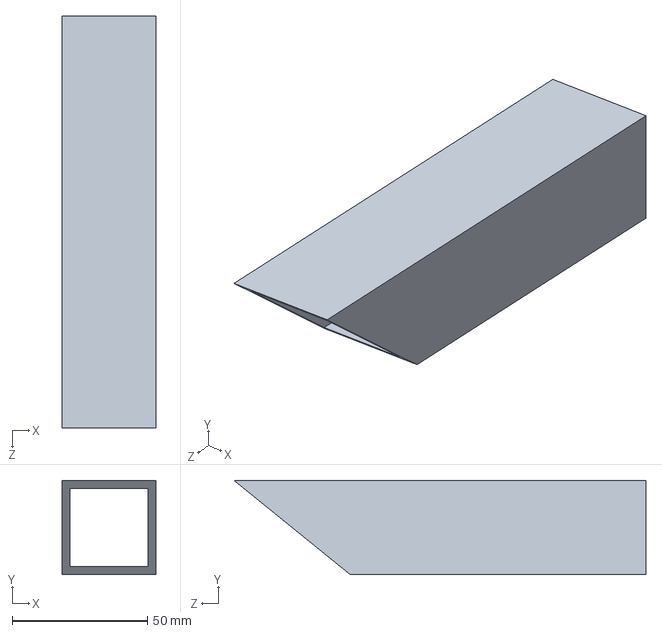
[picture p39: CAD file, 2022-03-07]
model/frame/1.25in_square_tube_0.50ft_cut.SLDPRT
34.8 x 34.8 x 152.4 mm

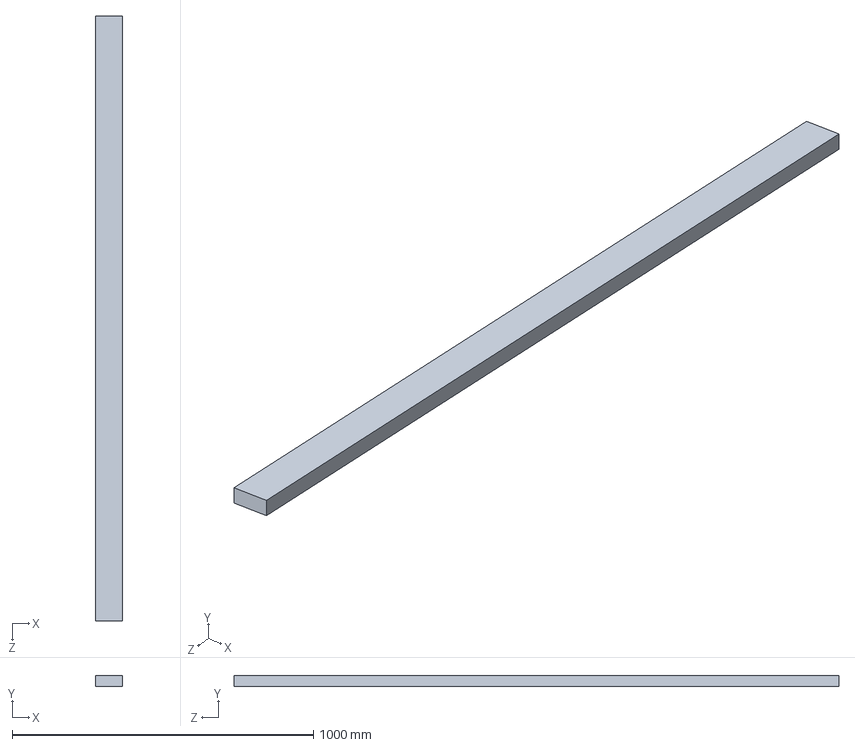
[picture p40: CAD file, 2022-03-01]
model/solar collecter/2x4in_length.SLDPRT
88.9 x 38.1 x 2007.9 mm

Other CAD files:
model/frame/1.5in_square_tube_5.5ft.SLDPRT
model/frame/1.25in_square_tube_1ft.SLDPRT
model/solar collecter/absorber.SLDPRT
model/frame/1.5in_square_tube_1ft.SLDPRT
model/drawings/absorber_plate.SLDDRW
model/drawings/collector_frame.SLDDRW
model/drawings/serpentine_manifold.SLDDRW
model/drawings/solar_collector.SLDDRW
model/frame/1.25in_square_tube_1.5ft.SLDPRT
model/frame/1.5in_square_tube_1.5ft.SLDPRT
model/frame/1.5in_square_tube_3ftt.SLDPRT
model/frame/1.5in_square_tube_4in.SLDPRT
model/solar collecter/2x4in_width.SLDPRT
model/solar collecter/epoxy.SLDPRT
model/solar collecter/serpentine_manifold.SLDPRT

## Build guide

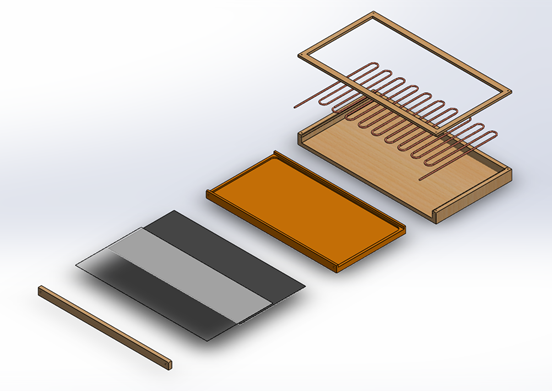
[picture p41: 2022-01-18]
documentation/TeX/images/collector_assembly_exploded.png

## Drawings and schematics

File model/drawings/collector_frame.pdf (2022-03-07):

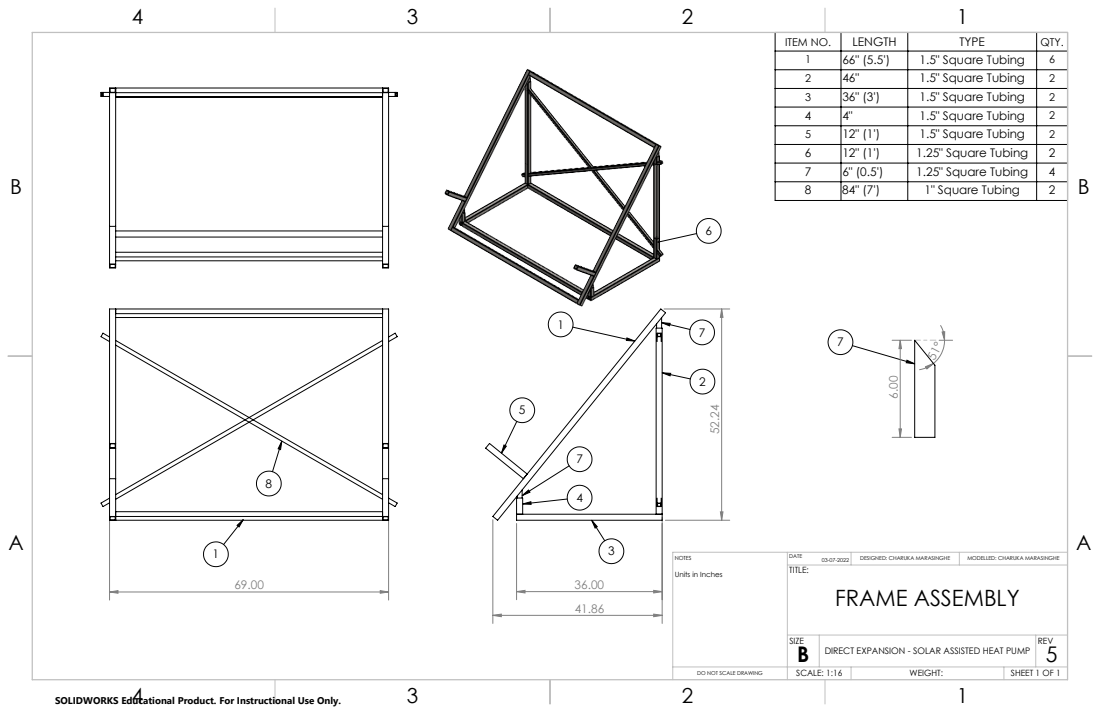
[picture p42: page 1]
FRAME ASSEMBLY; NOTES; DATE; DESIGNED: CHARUKA MARASINGHE; MODELLED: CHARUKA MARASINGHE

ITEM NO. | LENGTH | TYPE | QTY.
1 | 66" (5.5') | 1.5" Square Tubing | 6
2 | 46" | 1.5" Square Tubing | 2
3 | 36" (3') | 1.5" Square Tubing | 2
4 | 4" | 1.5" Square Tubing | 2
5 | 12" (1') | 1.5" Square Tubing | 2
6 | 12" (1') | 1.25" Square Tubing | 2
7 | 6" (0.5') | 1.25" Square Tubing | 4
8 | 84" (7') | 1" Square Tubing | 2

Units in Inches

SIZE B | DIRECT EXPANSION - SOLAR ASSISTED HEAT PUMP | REV 5

DO NOT SCALE DRAWING | SCALE: 1:16 | WEIGHT: | SHEET 1 OF 1

SOLIDWORKS Educational Product. For Instructional Use Only.

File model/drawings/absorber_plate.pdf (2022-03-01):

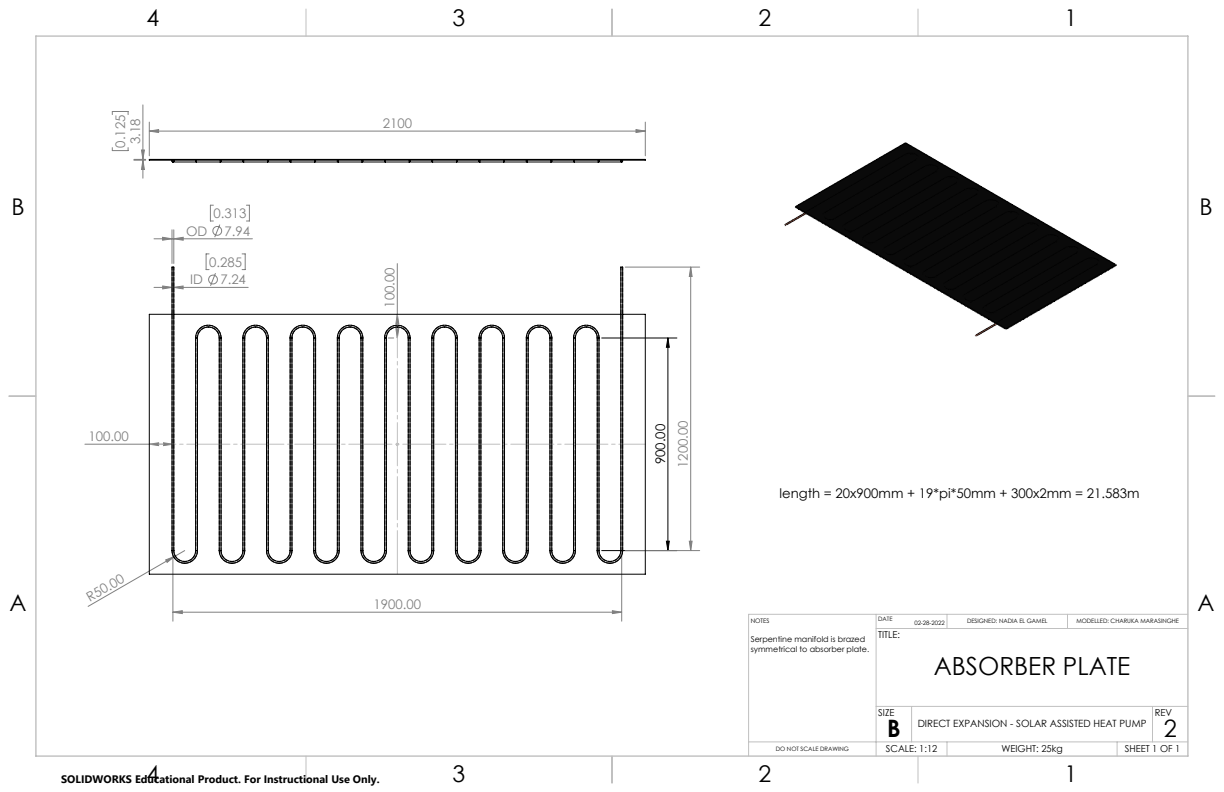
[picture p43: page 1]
length = 20x900mm + 19*pi*50mm + 300x2mm = 21.583m; ABSORBER PLATE; NOTES; DATE; DESIGNED: NADIA EL GAMEL; MODELLED: CHARUKA MARASINGHE

Serpentine manifold is brazed
symmetrical to absorber plate.

SIZE B | DIRECT EXPANSION - SOLAR ASSISTED HEAT PUMP | REV 2

DO NOT SCALE DRAWING | SCALE: 1:12 | WEIGHT: 25kg | SHEET 1 OF 1

SOLIDWORKS Educational Product. For Instructional Use Only.

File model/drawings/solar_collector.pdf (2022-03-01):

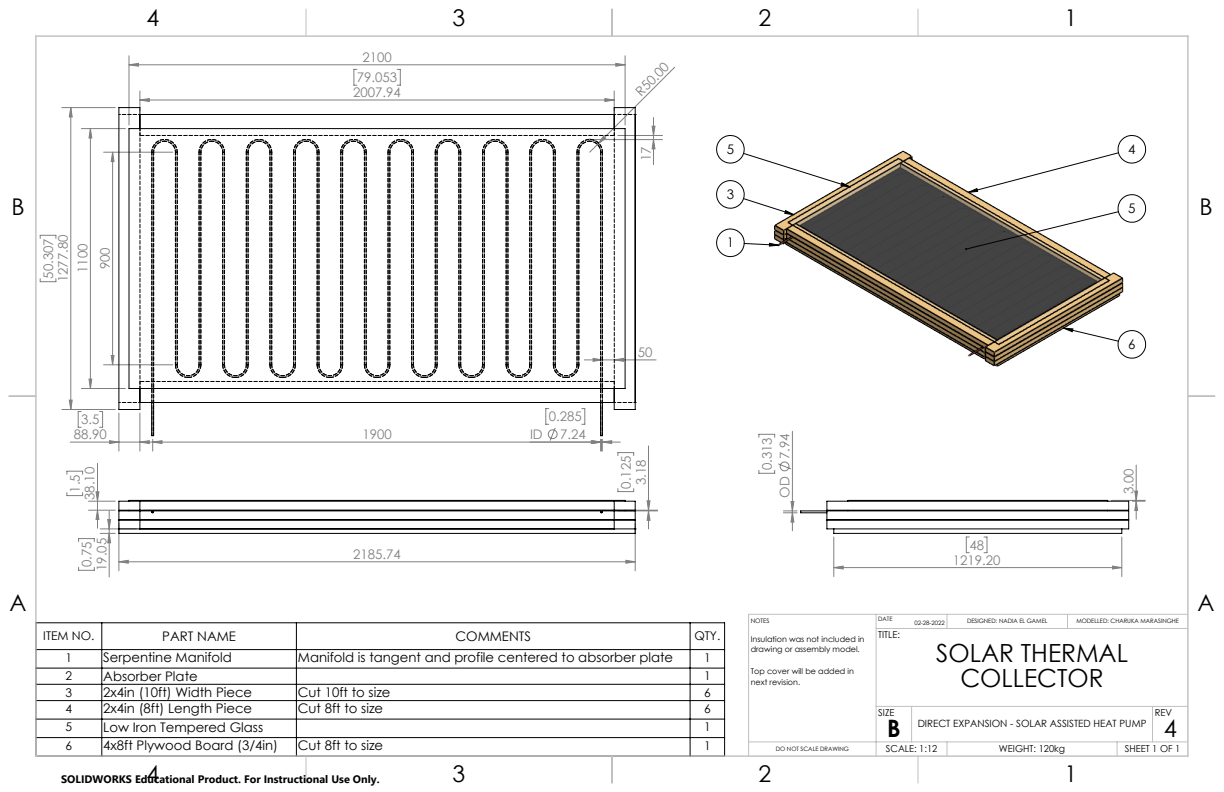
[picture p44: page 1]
SOLAR THERMAL; NOTES; DATE; DESIGNED: NADIA EL GAMEL; MODELLED: CHARUKA MARASINGHE

Insulation was not included in
drawing or assembly model.

ITEM NO. | PART NAME | COMMENTS | QTY.
1 | Serpentine Manifold | Manifold is tangent and profile centered to absorber plate | 1
2 | Absorber Plate | | 1
3 | 2x4in (10ft) Width Piece | Cut 10ft to size | 6
4 | 2x4in (8ft) Length Piece | Cut 8ft to size | 6
5 | Low Iron Tempered Glass | | 1
6 | 4x8ft Plywood Board (3/4in) | Cut 8ft to size | 1

Top cover will be added in
next revision.

SIZE B | DIRECT EXPANSION - SOLAR ASSISTED HEAT PUMP | REV 4

DO NOT SCALE DRAWING | SCALE: 1:12 | WEIGHT: 120kg | SHEET 1 OF 1

SOLIDWORKS Educational Product. For Instructional Use Only.

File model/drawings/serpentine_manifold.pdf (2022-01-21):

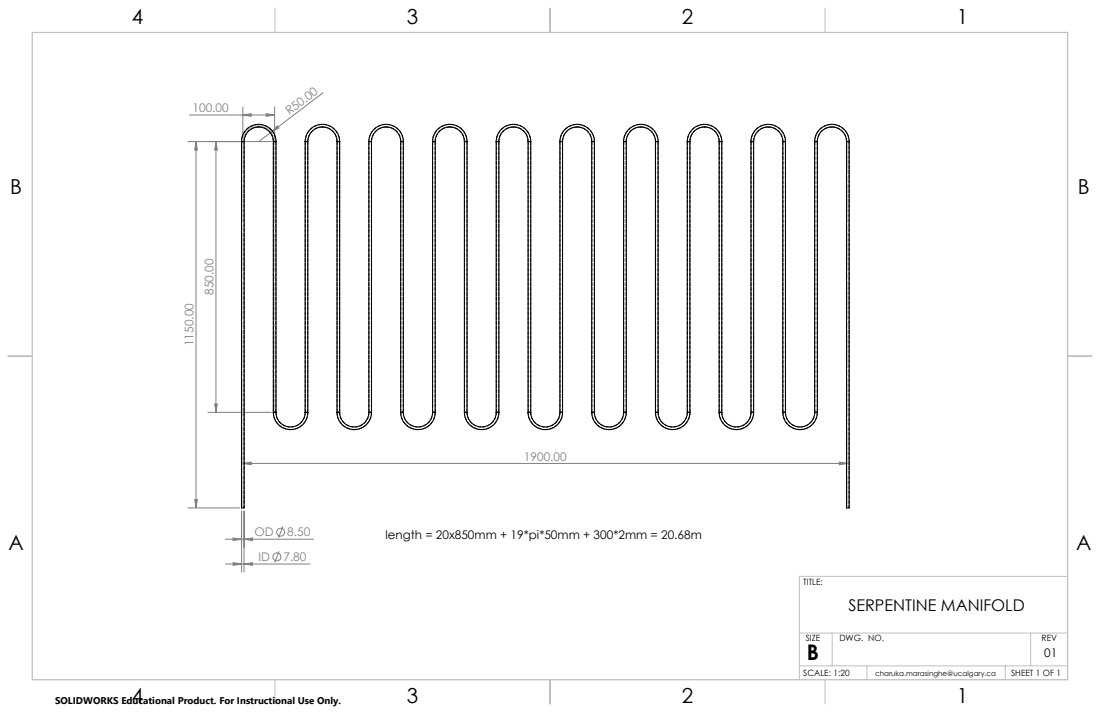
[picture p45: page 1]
length = 20x850mm + 19*pi*50mm + 300*2mm = 20.68m; SERPENTINE MANIFOLD

SIZE B | DWG. NO. | REV 01

SCALE: 1:20 | charuka.marasinghe@ucalgary.ca | SHEET 1 OF 1

SOLIDWORKS Educational Product. For Instructional Use Only.

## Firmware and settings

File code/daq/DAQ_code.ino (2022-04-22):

#include <OneWire.h>
#include <DallasTemperature.h>
#include <SPI.h>
#include <SD.h>
File myFile;
DateTime now;
int newHour = 0;
int oldHour = 0;
void save_temper

void save_temperature() { 
  myFile = SD.open("temp.txt", FILE_WRITE);
  now = rtc.now();
  myFile.print(now.hour());
  myFile.print(":");
  myFile.print(now.minute());
  myFile.print(",");
  
  for (int i = 2; i <5; i + 2) {
    // Data wire is plugged into pin 2 on the Arduino
    #define ONE_WIRE_BUS i
 
    // Setup a oneWire instance to communicate with any OneWire devices 
    // (not just Maxim/Dallas temperature ICs)
    OneWire oneWire(ONE_WIRE_BUS);
 
    // Pass our oneWire reference to Dallas Temperature.
    DallasTemperature sensors(&oneWire);
 
    void setup(void) {
      // start serial port
      Serial.begin(9600);
      Serial.println("Dallas Temperature IC Control Library Demo");

      // Start up the library
      sensors.begin();
    }

    sensors.requestTemperatures(); // Send the command to get temperatures
    myFile.print("Temperature is: ");
    myFile.print(sensors.getTempCByIndex(0)); 
    }

  myFile.close();
  }

void setup ()
{
Wire.begin();
rtc.begin();
Serial.begin(9600);
Serial.print("Initializing SD card...");
if (!SD.begin(10)) {
Serial.println("initialization failed!");
while (1);
}
Serial.println("initialization done.");
now = rtc.now();
oldHour = now.hour();
}

void loop () {
  now = rtc.now();
  newHour = now.hour();
  if (oldHour != newHour) {
    save_temperature();
    oldHour = newHour;
  }
}

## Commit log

2022-01-02 Add SOLIDWORKS model via upload
    [02absorber_assembly.SLDASM, Absorber.SLDPRT, Cover.SLDPRT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]
2022-01-21 Update model (#1)
    Updated model with variable dimensions
    Allows for quick changes to model when changing sizing.
    [02absorber_assembly.SLDASM, Absorber.SLDPRT, Cover.SLDPRT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]
2022-03-03 Revised frame to match standard sizes
    [1.5in_support_bracing_8ft.SLDPRT, 2.75in_square_tube_1.5ft.SLDPRT, 3_in_square_tube_1ft.SLDPRT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]
2022-03-04 Frame resize (#3)
    * Delete model/frame directory
    * Resized frame dimensions
    Using cold rolled square steel tubing with 1.5" walls
    [1.25in_square_tube_1.5ft.SLDPRT, 1.5in_square_tube_1.5ft.SLDPRT, 1.5in_square_tube_1ft.SLDPRT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]
2022-03-07 Updated frame assembly
    [1.25in_square_tube_0.50ft_cut.SLDPRT, 1.25in_square_tube_1ft.SLDPRT, 1.5in_square_tube_1ft.SLDPRT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]
2022-03-07 Updated frame drawing
    [collector_frame.SLDDRW]
2022-04-22 Updated DX-SAHP schematic
2022-04-22 Update DX-SAHP schematic
2022-04-22 Updated Gantt Chart
    [DX-SAHP_Gantt_Chart.xlsx]
2022-04-22 End of Project Updates (#4)
    * Update DX-SAHP schematic
    * Add files via upload
    * Updated tex files to final report
